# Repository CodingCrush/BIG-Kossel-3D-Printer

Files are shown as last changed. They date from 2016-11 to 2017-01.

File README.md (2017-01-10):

# 项目说明
这个是去年做的3d打印机清单，包括所有非标件及安装示意图。
效应器、两种57挤出机、滑车等非标件均为原创设计，开源供参考使用
按照物料清单买下来，成本2000-2500之内。不同的用料会有不同的成本
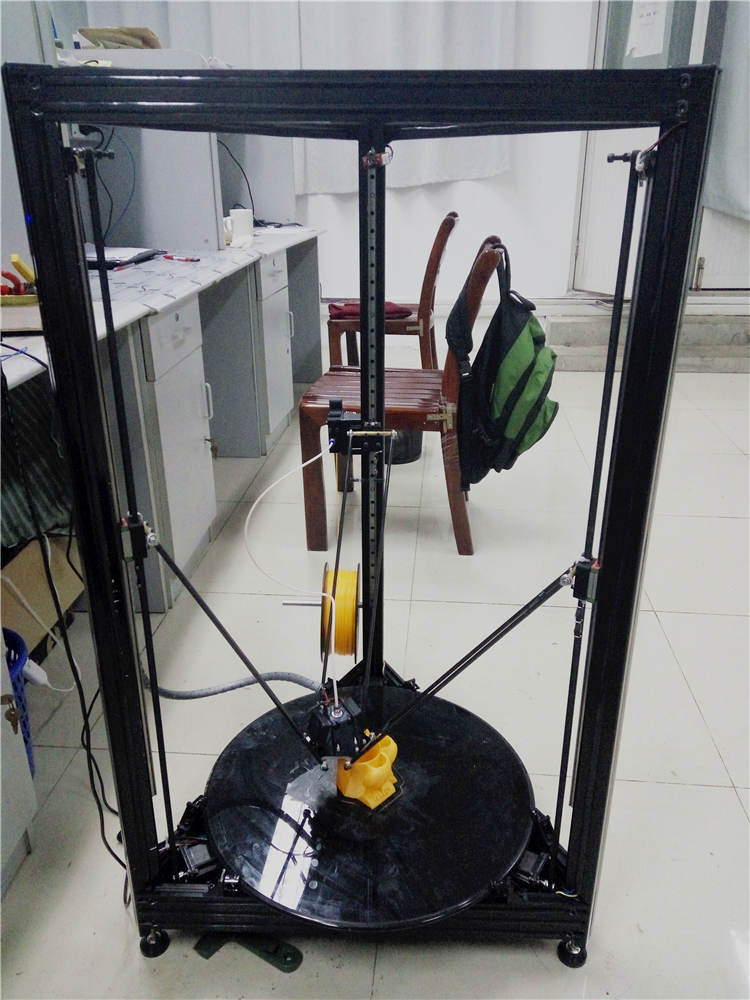
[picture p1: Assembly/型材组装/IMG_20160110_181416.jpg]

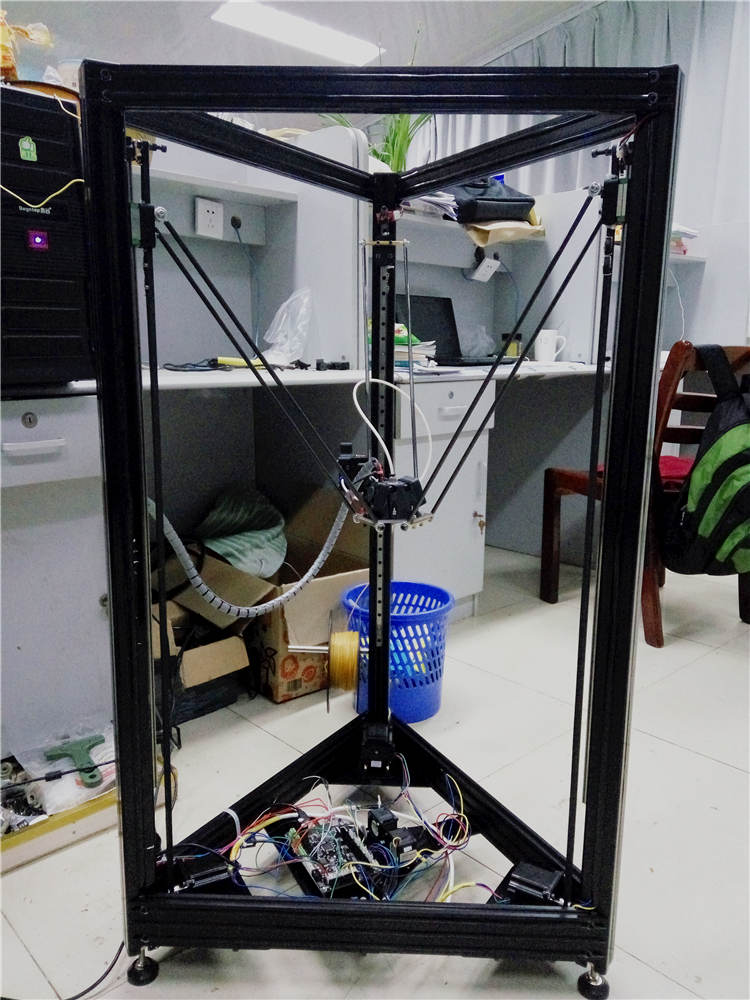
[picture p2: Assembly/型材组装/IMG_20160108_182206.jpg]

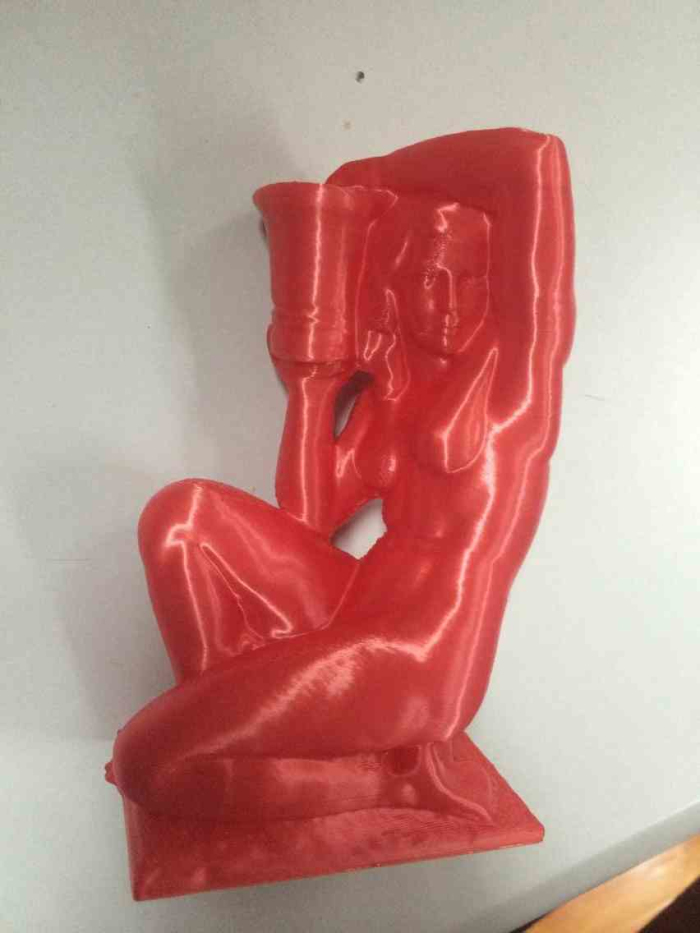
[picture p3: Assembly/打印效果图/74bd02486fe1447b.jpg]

# 成本预算：
框架300
线轨380
主板330
玻璃50
螺丝100
铁板加工件120
亚克力切割件30
轴承50
碳纤维管100
热床（可不选）200
步进电机100
电源50
导线20
其他配件100
齿轮皮带40
其他150
以上邮费200

# 关于效应器：
打印效果确实很棒，出风给喉管和打印件散热。两个12V的4010风扇在24V下超压使用。两侧进风在支架上部的密闭腔体内混合向下送出，密闭腔体相当于静压箱可以降低面风速的湍流度，同时降低面风速。充分保证散热效果。经过四次更新至V2.1版。

# 关于挤出机：
有42电机带韦德挤出与57电机直驱挤出的方案选择。42电机挤出力不够。即使买的行星减速也没那么神奇，不如一步到位，使用57电机直驱。更新至第五版，42mk8---42齿轮行星减速---42皮带减速行星减速---57mk8转接---57bowden。最后发现偷懒省钱都是浪费的开始。57直驱的挤出力强劲，打最小的鸟笼不会拉丝，回抽参数设的为130Mm/s 7mm；

# 挤出机对比
Mk8挤出机的缺点：直齿轮坑料，42电机发热大融料；
42wade齿轮减速挤出机缺点：回抽噪音大，回抽速度不高；
42wade皮带减速挤出机缺点：噪音小，回抽速度依然不高，皮带有可能打滑；
57_mk8挤出机缺点：暂无
57_bowden挤出机缺点：暂无

# 关于成型空间：
我最初做的是1050mm立柱的。打印高度是500mm ，直径是450mm高度。
关于打印效果：
全金属结构保证整机刚性；
32位主板保证运算不顿卡；
堆叠双凤道效应器保证打印件散热强力；
线性导轨保证三轴运动的直线度挤出稳定；
57挤出机保证挤出的力矩和回抽质量；
打印效果和用料息息相关。想省钱又想有好的打印效果是不可能的

# 关于E3D-V6：
请严格安装图上的分开购买，切勿购买套件V6。原版的V6非常容易堵头。
正确安装E3D-V6的方式：
首先将喷嘴拧到加热块上，拧到底，然后回退一圈；
拧上喉管、散热器，用手拧紧，切勿大力，喉管脆弱。容易折断；
联机加热至200度，用扳手固定住加热块，用老虎钳狂拧喷嘴到拧不动为止；
安装教程[参考](http://wiki.e3d-online.com/wiki/E3D-v6_Assembly)：

# 关于固件调试：
我写了三份调试教程：
8位MEGA2560的marlin固件；
32位due的repetier固件；
Mks sbase的smoothieware固件；

配合KOSSEL吧精品帖理解研究

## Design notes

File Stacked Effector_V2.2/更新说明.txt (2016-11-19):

V2.2版本

1.增加30风扇支架
2.取消带走线孔的40风扇支架，加热棒和热敏电阻从效应器下方走线。
3.原E3D固定支架的沉孔不方便在拧螺丝时固定螺母，紧固效果不佳。已经修正
4.使用MGN12H微轨，打印MGN12底座即可。

优点：
我设计的这款双风道效应器实测打印效果很棒。上层的空腔的作用相当于一个静压箱，给两侧进风混合用的，向下出风的面风速湍流度低，散热效果很均匀。试试就不会后悔的
缺点：
必须在切片软件里设置风扇始终运行，第一层风速可以设置的低一点。
不便拆卸。

如果具备加工条件，可以将底座改为铝板+铜柱的设计。铜柱选择M4 50MM长度的，开M3的孔，距离为20mm。

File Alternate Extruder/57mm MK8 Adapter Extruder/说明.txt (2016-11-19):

电机座，带42电机的转接孔，可以安装MK8挤出机或者bowden挤出机
mk8挤出机需要改造齿轮与轴承。直齿轮啃料太过凶猛，所以改造成mk7齿轮和内4外10或12的轴承。
mk8走线管模型是因为mk8从齿轮到进料口的距离太长，高速挤出下容易折弯，所以加入一个螺纹套。减少变形

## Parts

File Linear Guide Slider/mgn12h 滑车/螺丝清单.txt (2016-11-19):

M4 25MM 2个
M3 25MM 4个 及垫片
M4 方螺母2个
M4 铜螺母2个

线轨固定需要
m3 8mm 及20 m3 T螺母 
具体数量自定 

导轨螺孔间距为20mm

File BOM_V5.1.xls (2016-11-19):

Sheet: 安装流程
步序 | 操作
1 | 熟读物料清单；
2 | 确定自己所需机子的高度，根据需求自主提高或降低高度；
3 | 购买铝合金框架、上下铁板连接件、螺丝五金配件等；
4 | 购买线轨；
5 | 制作推杆；
6 | 组装框架线轨玻璃等；
7 | 购买电子配件；
8 | 打印所需非标件；
9 | 再次安装，确定缺少的螺丝数量及长度；
10 | 再次购买螺丝；
11 | 完全安装；
12 | 调试并打印；
所需打印件
滑车 | MGN12滑车 | 3 | 必须需要
 | MGN12滑车盖板 | 3
限位开关 | 9MM/19MM孔距 | 3
2.1版堆叠效应器 | MGN12H底座 | 1
 | E3D支座 | 1
 | 40MM风扇支座 | 2
57_bowden挤出机 | 摇臂 | 1
 | 支座 | 1

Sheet: 框架清单
名称 | 型号 | 数量 | 备注
主体框架
4040氧化黑色欧标铝 | 加工方式见图纸 | 3 | 将铝型材加工图纸发送给客服qq 3307599979，然后购买。大概300元（不含邮费）
2060氧化黑色欧标铝 |  | 3
2040氧化黑色欧标铝 |  | 3
激光切割件，分为两部分
亚克力切割件 | 见图纸 |  | https://item.taobao.com/item.htm?spm=a1z09.2.0.0.DWjkuu&id=20099696260&_u=9b3kpon8ca8 | 大概30元不含邮费
铁板切割件 | BOM默认选择57步进电机底座 |  | https://item.taobao.com/item.htm?spm=a1z09.2.0.0.k5vPzQ&id=40188190385&_u=jb3kpon455d | 大概120元不含邮费
与上面一样，将图纸发给卖家购买
mgn12h线轨套件以及同一家店可以买的
直线导轨MGN12 | 800mm | 3 | https://item.taobao.com/item.htm?spm=a1z09.2.0.0.LKU8Oa&id=26759568854&_u=eb3kpona8c6 | 130一米
导轨滑块 | MGN12H | 3 |  | 28一个
8MM光轴 | 200mm | 1 | https://item.taobao.com/item.htm?spm=a1z10.5-c.w4002-1865926650.40.Pj0TRl&id=18726450513 | 用作料架
光轴支架 | sk8 | 1 | https://item.taobao.com/item.htm?spm=a1z10.5-c.w4002-1865926650.27.MxqcvY&id=18625133704
尼龙定向调节脚 | D40 M8 50MM | 3 | https://item.taobao.com/item.htm?spm=a1z10.5-c.w4002-1865926650.35.BtjLvI&id=38758004319 | 立柱安装的蹄脚
玻璃、固定、以及热床
钢化玻璃平台 | 500mm直径，10mm厚度 | 1 | https://item.taobao.com/item.htm?spm=a1z09.2.0.0.mM9U3M&id=44221134157&_u=ub3kpon85cc
玻璃层夹 | 夹6-10mm玻璃 | 6 | https://item.taobao.com/item.htm?spm=a1z09.2.0.0.mM9U3M&id=16613643636&_u=ub3kpon79ec
玻璃贴膜 | 黑色不透光50X100 | 1 | https://item.taobao.com/item.htm?spm=a1z09.12.0.0.oPNmCq&id=35529763436&_u=eb3kpon4e8c
固体胶 | 7092固体胶 | 1 | https://detail.tmall.com/item.htm?spm=a230r.1.14.15.UjnPbe&id=521067459509&ns=1&abbucket=19
硅橡胶加热板热床 | D=450MM | 1 | https://item.taobao.com/item.htm?spm=a1z09.2.0.0.JIdvOC&id=524124462678&_u=eb3kpon2f34
热床200包邮，我买的是220V 150W的固定功率热床，表面温度大概可以达到60摄氏度。根据经济实力决定是否购买
推杆、轴承 |  |  |  | 外部可以套上彩色热缩管
铝管 | 内径4MM 外径 6MM,450MM长度 | 6 | https://item.taobao.com/item.htm?spm=a1z09.2.0.0.ZB8lGC&id=41292505365&_u=1b3kpond9cf
碳纤维管 | 内径4MM 外径 6MM,450MM长度 | 6 | https://item.taobao.com/item.htm?spm=a1z09.2.0.0.V9akuZ&id=38251842903&_u=eb3kpon99a4 | 用AB胶固定
铝管大概20块，碳纤维大概100块。一个不好看不抗弯，一个好看抗弯。根据经济实力决定买哪个
挤出机用轴承 | 608ZZ | 1 | https://item.taobao.com/item.htm?spm=a1z10.3-c.w1017-2093055617.16.R8DyGV&id=16485904719&
鱼眼杆端关节轴承 | SA4/T | 12 | https://item.taobao.com/item.htm?spm=a1z10.3-c.w1017-2093055617.54.vsEDZy&id=16076773170&
惰轮用法兰轴承 | MF105ZZ | 6 | https://item.taobao.com/item.htm?spm=a1z10.3-c.w1017-2093055617.48.7UzuTb&id=21102608035&
线材以及同一家店可以买到的
导线 | 黑黄蓝红 | 各5m | https://item.taobao.com/item.htm?spm=a1z09.2.0.0.0SBSik&id=23540708099&_u=eb3kpon026b
XH2.54接插件 | 2P | 1 | https://item.taobao.com/item.htm?spm=a1z09.2.0.0.0SBSik&id=14476357944&_u=eb3kpone20c
 | 3P | 1 | https://item.taobao.com/item.htm?spm=a1z09.2.0.0.0SBSik&id=14473394032&_u=eb3kponfa8b
 | 4P | 1 | https://item.taobao.com/item.htm?spm=a1z10.3-c.w4002-12998195972.51.XmKiKG&id=14476473424
热缩管 | 3mm直径 | 5m | https://item.taobao.com/item.htm?spm=a1z10.3-c.w4002-12998195972.12.nhstYa&id=13996979237
电源插头 | 2脚 | 1 | https://item.taobao.com/item.htm?spm=a1z10.3-c.w4002-12998195972.80.4smjrb&id=20905900482
AB胶 |  | 1 | https://item.taobao.com/item.htm?spm=a1z10.3-c.w4002-12998195972.9.vEEsrS&id=36276164986

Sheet: 配件清单
名称 | 型号 | 数量 | 链接 | 备注
电源
24V开关电源 | 24V 4.5A | 1 | https://detail.tmall.com/item.htm?id=37030219054&ali_trackid=1_5102b68adeeb74cf0f9209195d0a94c7
32位主板方案
MKS SBASE V1.1 | SMOOTHIEBOARD | 1 | https://item.taobao.com/item.htm?spm=a230r.1.14.9.vgDiJN&id=44718074273&ns=1&abbucket=15#detail | 推荐用32位，8位效果不行。一步到位不要瞎折腾
显示屏 | 12864 | 1 | https://item.taobao.com/item.htm?spm=a1z10.5-c.w4002-3498108424.13.ABPwxh&id=36373394177
显示屏延长线 | 10pin 60cm | 1 | https://item.taobao.com/item.htm?spm=a1z10.3-c.w4002-3498109524.9.ptclZO&id=40086051115
E3D-V6 1.75mm 喷头套件
喉管 | 4.1改进版 | 1 | https://item.taobao.com/item.htm?spm=a1z10.5-c.w4002-11935848136.17.evg1rh&id=44465372886 | 不建议购买E3DV6套件，价格贵并且还需要单独改造
喷嘴 | 一般为1.75MM/0.4 | N | https://item.taobao.com/item.htm?spm=a1z10.5-c.w4002-11935848136.34.nrbVxR&id=44358306425 | 喷嘴属于易耗品，建议买三四个备用
加热块 | E3D-V6 | 1 | https://item.taobao.com/item.htm?spm=a1z0d.6639537.1997196601.16.l5Cwhh&id=42040453133
V6散热器 | 远程通用 | 1 | https://item.taobao.com/item.htm?spm=a1z0d.6639537.1997196601.24.l5Cwhh&id=44405326311
12V 40W 加热棒 | 24V | 1 | https://item.taobao.com/item.htm?spm=a1z0d.6639537.1997196601.32.l5Cwhh&id=40297664127
热敏电阻 | NTC 100k | 1 | https://item.taobao.com/item.htm?spm=a1z0d.6639537.1997196601.40.l5Cwhh&id=40254167255
直通快拆 |  | 1 | https://item.taobao.com/item.htm?spm=a1z0d.6639537.1997196601.56.l5Cwhh&id=42054728629 | 必须要，可有效减少拉丝
普通快拆 | PC4-M6 | 1 | https://item.taobao.com/item.htm?spm=a1z10.3-c.w4002-11935848131.29.ZmzM5A&id=520893975535
57挤出机
步进电机 | 57/出轴8MM | 1 | https://item.taobao.com/item.htm?spm=a1z0d.6639537.1997196601.4.DnqXQb&id=40165378221
步进电机支座 | 57 | 1 | https://item.taobao.com/item.htm?spm=a1z10.3-c.w1017-2775512882.16.UAF9zR&id=40276550667&
42步进电机
步进电机减震器 | 42步进电机减震 | 1 | https://item.taobao.com/item.htm?spm=a1z10.3-c.w4002-5542399676.10.WlW5mC&id=41871297943
步进电机 | 42 | 3 | https://item.taobao.com/item.htm?spm=a1z0d.6639537.1997196601.198.3fQ353&id=520141390607 | 要求拆除带轮
8MM挤出齿轮以及皮带
mk7 齿轮 | 1.75/内孔8MM | 1 | https://item.taobao.com/item.htm?spm=a230r.1.14.73.4LRCcv&id=43350287703&ns=1&abbucket=17#detail
皮带 | 2gt/6mm | 7m | https://item.taobao.com/item.htm?spm=a1z10.5-c.w4002-4073923749.44.Nxt9Df&id=35878681904
其他配件
皮带张力弹簧 |  | 10 | https://item.taobao.com/item.htm?spm=a1z09.2.0.0.ZB8lGC&id=40715365020&_u=1b3kpond30a | 一次装一个，多6个备用，用久了弹力损失
拉杆弹簧 |  | 10 | https://item.taobao.com/item.htm?spm=a1z09.2.0.0.ZB8lGC&id=44068679730&_u=1b3kponee4c | 中间拉成范性形变，否则力道太大，拉杆会变形
散热风扇 | 4010 | 5 | https://item.taobao.com/item.htm?spm=a1z09.2.0.0.ZB8lGC&id=40335881133&_u=1b3kpon0285 | 2个做效应器，2个吹主板，剩1个吹挤出机或备用
四氟管 | PTFE 内2 外4 | 1m | https://item.taobao.com/item.htm?spm=a1z10.3-c.w4002-11935848131.19.E6PGeQ&id=44357906558
降压模块 | LM2596 | 1 | https://item.taobao.com/item.htm?spm=a1z0d.6639537.1997196601.41.zaBsTh&id=40019604731 | 吹主板的风扇降压，24V IN ，12V out。工作在24V太吵。效应器风扇则需要超压使用，否则风力不足
挤出机弹簧 |  | 3 | https://item.taobao.com/item.htm?spm=a1z09.2.0.0.udr64W&id=42750895769&_u=nb3kpon16d7
限位开关 | 19mm孔距 | 3 | https://item.taobao.com/item.htm?spm=a1z09.2.0.0.iTCYy6&id=39937698796&_u=eb3kpon373c
步进电机支座 | 42 | 3 | https://item.taobao.com/item.htm?spm=a1z10.3-c.w4002-11935848131.9.PmEVYh&id=39937902501
2gt同步带轮 | 16齿/5mm | 3 | https://item.taobao.com/item.htm?spm=a1z10.3-c.w4002-11935848131.11.RbJe5L&id=39890812501
包邮类
绕线管 | 黑色 | https://item.taobao.com/item.htm?spm=a230r.1.14.38.aUPH6V&id=45706578890&ns=1&abbucket=8#detail
主板TF卡 | 2g | https://item.taobao.com/item.htm?spm=a230r.1.14.1.p7Qztg&id=524953996445&ns=1&abbucket=8#detail
USB打印线 | 3m | https://detail.tmall.com/item.htm?id=10923587984&cm_id=140105335569ed55e27b&abbucket=8&skuId=50238254065
自喷漆 | 黑色 | https://detail.tmall.com/item.htm?id=520129085679&cm_id=140105335569ed55e27b&abbucket=8&skuId=3100609580236
铲刀 | BT-L120 | https://detail.tmall.com/item.htm?id=45471830184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

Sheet: 螺丝清单
40&20型材间连接，以下内六角螺丝基本在宇昊通五金店都能找到
M5 14MM | 24 | https://item.taobao.com/item.htm?spm=a1z09.2.0.0.Be0ikY&id=16463536281&_u=eb3kponf473
40_M5滑块螺母 | 24 | https://item.taobao.com/item.htm?spm=a1z09.2.0.0.Be0ikY&id=15146235453&_u=eb3kpon8b90
MGN12H固定，注意摆放居中。小心安装，槽宽较大。40_M3螺母奇货可居
M3 12MM | 15
40_m3滑块螺母 | 15 | https://buyertrade.taobao.com/trade/itemlist/list_bought_items.htm?spm=2013.1.1997525045.2.vBxTNu
玻璃固定
2028角码 | 6 | 一共固定6个玻璃层夹
M5 10MM | 12
20_M5_T螺母 | 6
M5螺母 | 6
M5 垫片 | 18
57_bowden挤出机
M3 50MM | 1 | 螺丝、挤出臂、电机座、弹簧、螺母依次固定。抗弯用
M5 8MM | 2
M4 50MM | 4 | 固定到电机座上，其中右上角固定时中间加一弹簧
M8 16MM圆柱销 | 1 | https://item.taobao.com/item.htm?spm=a1z09.2.0.0.49Pr58&id=37496544497&_u=eb3kpon8f8e
M4 25MM | 2
PC4-M6扁螺母 | 2 | https://item.taobao.com/item.htm?spm=a1z09.2.0.0.49Pr58&id=38609743045&_u=eb3kponab8b
M4 50蝶形螺丝 | 2 | https://item.taobao.com/item.htm?spm=a1z09.2.0.0.49Pr58&id=39064367809&_u=eb3kpon3ad6
40_M4_T螺母 | 2 | 固定电机座
M4 10MM | 2
M4方螺母 | 4
42_步进电机
M4 12MM | 12 | 固定步进电机座到铁板上
M4螺母 | 12
M5 8MM | 12 | 固定铁板到20型材上
20_M5_T螺母 | 12
M3 12MM | 6 | 固定减震垫到电机座上
M3螺母 | 6
M3 10MM | 6 | 固定步进电机到减震垫上
惰轮的固定
2028角码 | 3 | 把角码固定在铁板上
M5 10MM | 3
M5螺母 | 3
M5 8MM | 12 | 固定铁板到20型材上
20_M5_T螺母 | 12
M5 50MM 全牙 | 3 | https://item.taobao.com/item.htm?spm=a1z10.3-c.w4002-9022202682.74.5PrEE9&id=16566972853
M5螺母 | 18 | 固定长螺丝
线轨滑车铜柱版和非铜柱版共同所需螺丝 |  |  | 铜柱需要自己加工打孔，间距为20mm，打孔M3
M4 20MM | 6
M4方螺母 | 6 | M4*7*2(碳钢镀彩锌)
M3 25MM | 12 | 加垫片
M3 20mm | 6
M4铜螺母 | 6 | https://item.taobao.com/item.htm?spm=a1z10.3-c.w4002-9022202682.35.IZaODN&id=4394094562
M4 40MM双通铜柱 | 6 | https://item.taobao.com/item.htm?spm=a1z10.3-c.w4002-12153267213.26.eVsX5I&id=44046619758
堆叠式效应器铜柱版和非铜柱版共同所需螺丝
M4 20MM | 6 | 固定鱼眼
M4铜螺母 | 6
M4方螺母 | 6
M3 50MM | 2 | 固定两片E3D支座
M3 25MM | 4 | 固定E3D支座
M3 15MM | 8 | 固定4010风扇
M3 15MM | 4 | 固定风扇支架
M3螺母 | 4 | 风扇支架卡住的螺丝
M4 50MM双通铜柱 | 6 | https://item.taobao.com/item.htm?spm=a1z10.3-c.w4002-12153267213.26.eVsX5I&id=44046619758
主板及亚克力固定所需螺丝
M5 8MM | 3 | 固定亚克力到20型材上
20_M5_T螺母 | 3
M3*6+6单通铜柱 | 6 | https://item.taobao.com/item.htm?spm=a1z10.3-c.w4002-9022202682.9.PBuRxQ&id=14854113926
M3螺母 | 12 | 固定铜柱到亚克力板上
M3 8MM | 6 | 固定主板和降压板到铜柱上
2028角码 | 1 | 固定风扇支架到亚克力上
M5 10MM | 2
M5螺母 | 2
M3 20MM | 8 | 固定风扇到风扇支架上
M3螺母 | 8
限位开关固定
30_M4_T螺母 | 3 | 固定限位开关支座到40型材上
M4 10MM | 3
M3 8MM | 6 | 固定限位开关到支座上
装饰平封条
20系列平封条 | 18m | https://item.taobao.com/item.htm?spm=a1z09.2.0.0.ZB8lGC&id=43861741264&_u=1b3kpon28bf
黑色40系列平封条 | 10m | https://item.taobao.com/item.htm?spm=a1z09.2.0.0.49Pr58&id=43825390300&_u=eb3kpon36ad
4040盖板 | 3 | https://item.taobao.com/item.htm?spm=a1z09.2.0.0.iTCYy6&id=41300397509&_u=eb3kpon2bbd

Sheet: 42wade(供参考)
名称 | 型号 | 数量 | 链接 | 备注
绞丝轴 |  | 1 | https://item.taobao.com/item.htm?spm=a1z09.2.0.0.udr64W&id=40386340875&_u=nb3kpona52b
弹簧 |  | 2 | https://item.taobao.com/item.htm?spm=a1z09.2.0.0.udr64W&id=42750895769&_u=nb3kpon16d7
轴承 | 608ZZ | 3 | https://item.taobao.com/item.htm?spm=a1z09.2.0.0.udr64W&id=42879447860&_u=nb3kpon72ef
无头机米螺丝 | M4 10MM | 2 | https://item.taobao.com/item.htm?spm=a1z0d.6639537.1997196601.34.n9pQzp&id=36267353233 | 固定电机小齿轮
螺母 | M4 | 2
 | M3 20MM | 3 |  | 固定42电机
 | M3 25MM | 1
 | M3 螺母 | 1 |  | 固定摇柄
 | M4 60MM | 2 |  | 固定弹簧
 | M4扁螺母或方螺母 | 2
 | M4蝶形螺母 | 2 | https://item.taobao.com/item.htm?spm=a1z0d.6639537.1997196601.44.n9pQzp&id=35480309874
 | M8 螺母 | 1
 | 扁M6 螺母 | 1 | https://item.taobao.com/item.htm?spm=a1z0d.6639537.1997196601.64.n9pQzp&id=37376708205 | 固定PC4-M6
圆柱销 | m8 16MM | 1 | https://item.taobao.com/item.htm?spm=a1z0d.6639537.1997196601.14.n9pQzp&id=35470507276
推荐使用57直驱挤出机，该方案供已有42电机作挤出机的使用。因为42电机扭矩不足，直驱容易失步，所以需要齿轮减速
42步进电机 | 身长不限，用作挤出机 | 1 | 韦德挤出机
42电机支座 |  | 1 | https://item.taobao.com/item.htm?spm=a1z09.2.0.0.ZB8lGC&id=39937902501&_u=1b3kpon197f | 固定挤出机

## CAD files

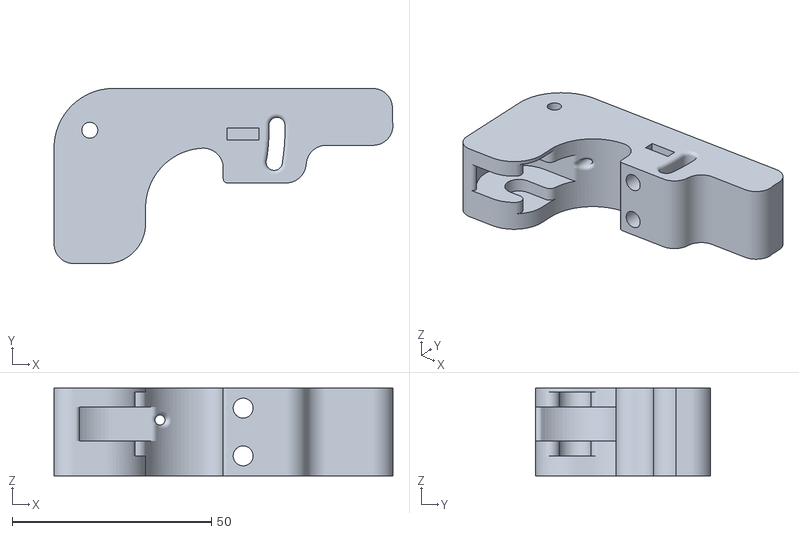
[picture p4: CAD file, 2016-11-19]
57mm Bowden Extruder/挤出臂，走线偏离中心3mm.stl
85.1 x 44.0 x 22.0

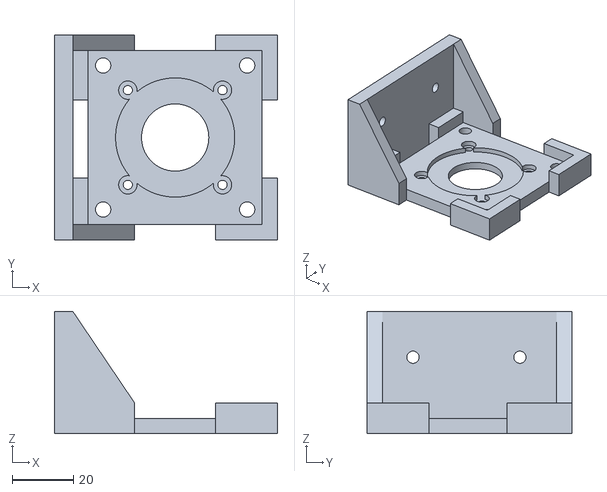
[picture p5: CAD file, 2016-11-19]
Alternate Extruder/57mm MK8 Adapter Extruder/57电机座.stl
73.0 x 67.0 x 40.0

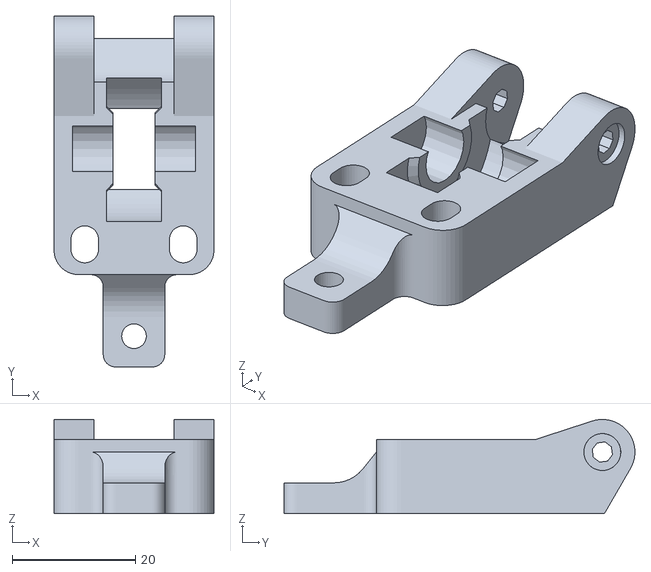
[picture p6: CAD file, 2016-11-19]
Alternate Extruder/Improved 42mm Wade Extruder/M4_Guidler_2.stl
26.0 x 57.0 x 15.3

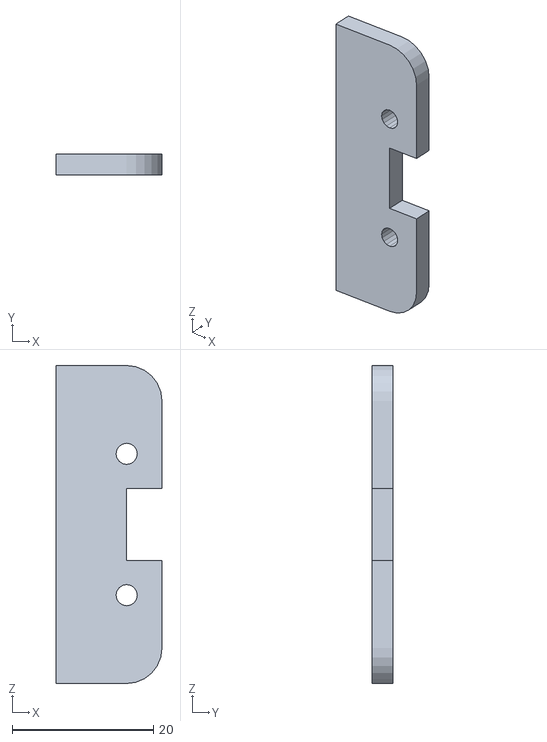
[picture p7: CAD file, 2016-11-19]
Linear Guide Slider/mgn12h 滑车/mgn12h_盖板.stl
15.0 x 3.00 x 45.0

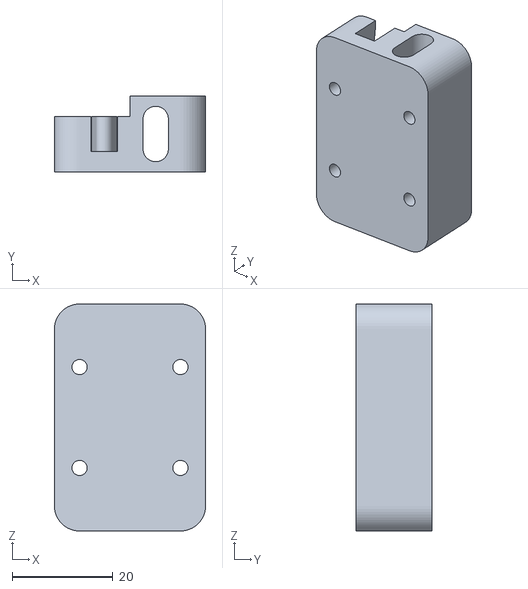
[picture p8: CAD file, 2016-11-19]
Linear Guide Slider/mgn12h滑车（需配合铜柱）/mgn12h_carriage.stl
30.0 x 15.0 x 45.0

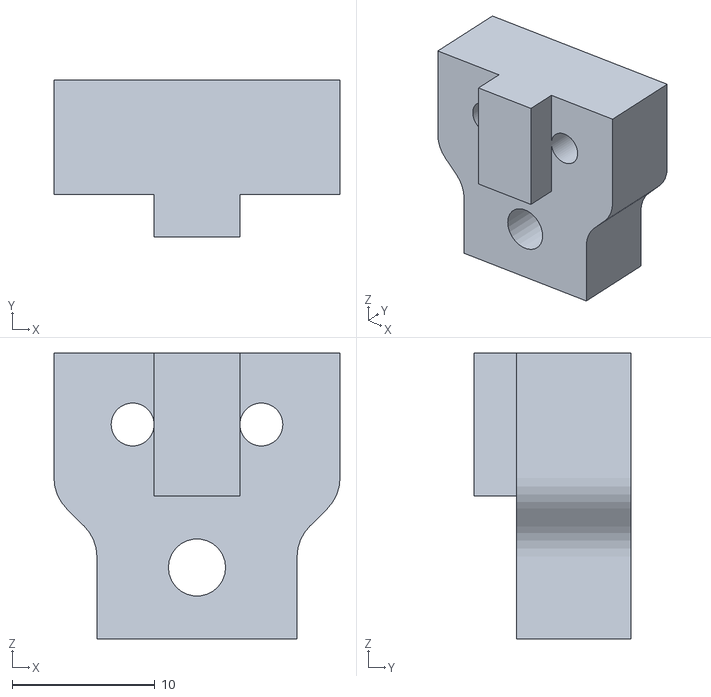
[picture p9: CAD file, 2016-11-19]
Mechanical Limit Switch Holder/mgn12h_9mm.stl
20.0 x 11.0 x 20.0

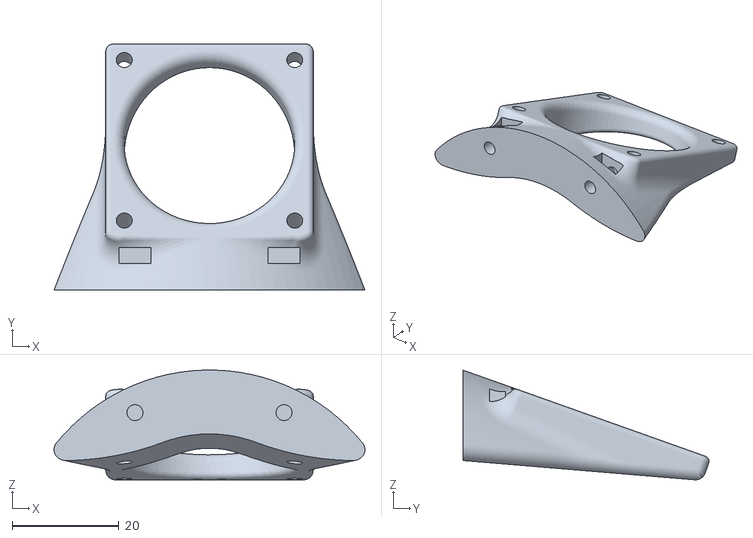
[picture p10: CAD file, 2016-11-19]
Stacked Effector_V2.2/40风扇支架.stl
58.4 x 46.2 x 20.6

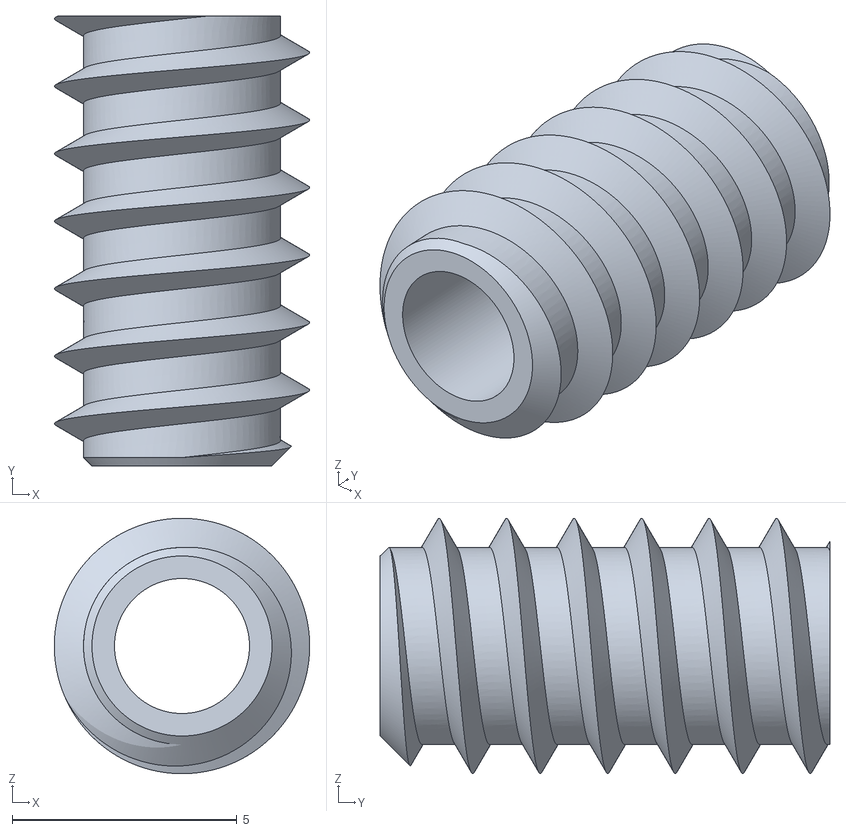
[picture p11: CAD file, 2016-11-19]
Alternate Extruder/57mm MK8 Adapter Extruder/M6螺纹套.stl
5.68 x 10.0 x 5.68

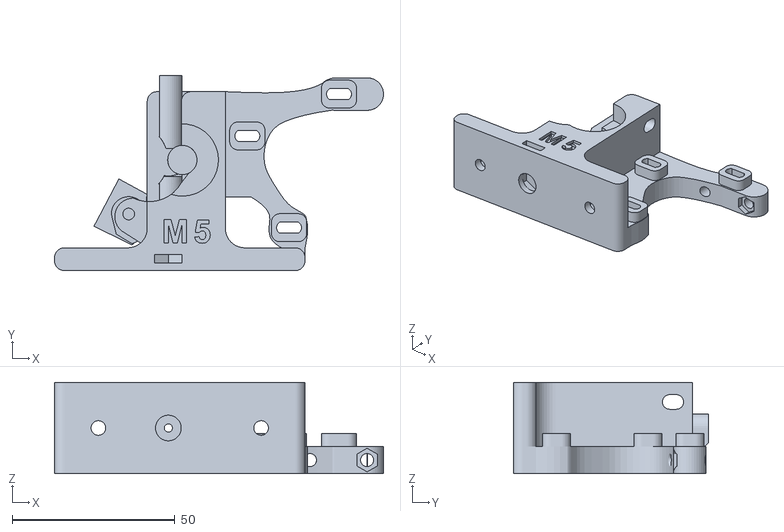
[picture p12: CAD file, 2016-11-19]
Alternate Extruder/Improved 42mm Wade Extruder/extruder_bowdenM5.stl
101.1 x 60.0 x 28.0

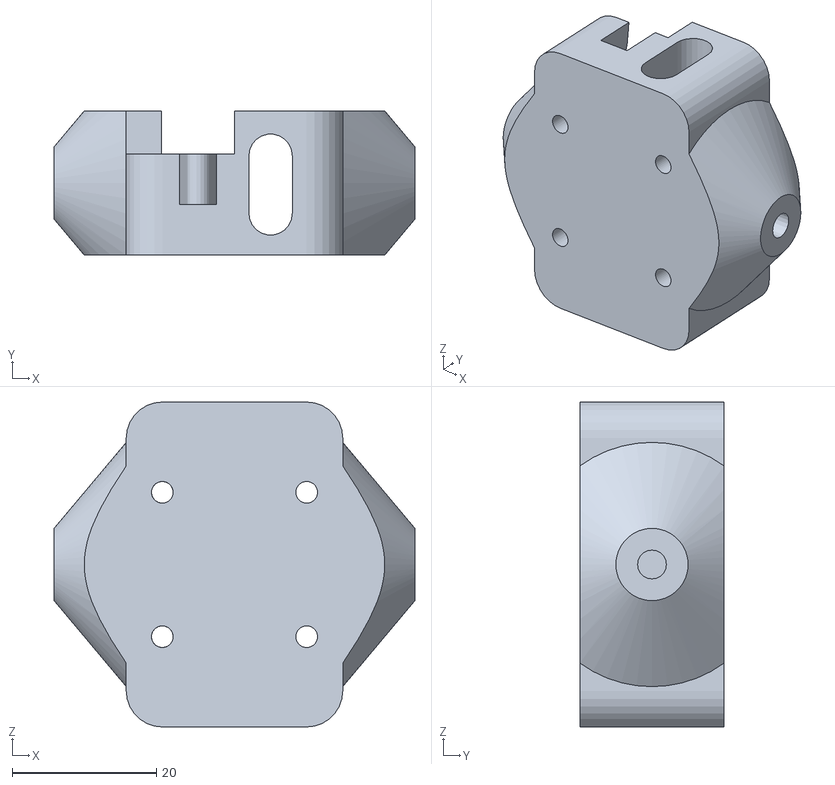
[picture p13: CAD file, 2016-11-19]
Linear Guide Slider/mgn12h 滑车/mgn12h_滑车.stl
50.0 x 20.0 x 45.0

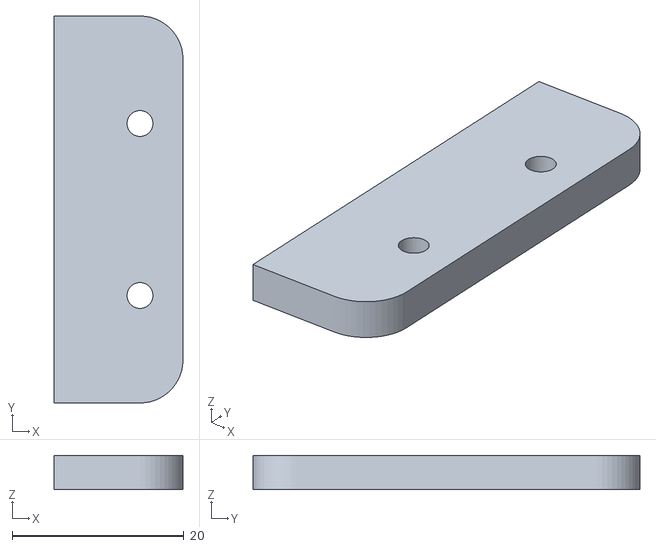
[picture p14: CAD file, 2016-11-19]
Linear Guide Slider/mgn12h滑车（需配合铜柱）/gaiban.stl
15.0 x 45.0 x 4.00

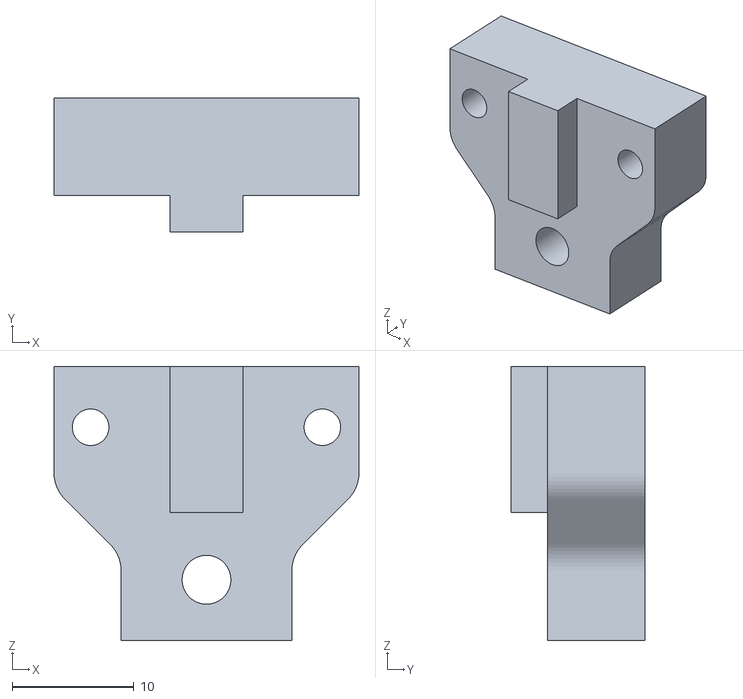
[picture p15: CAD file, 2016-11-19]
Mechanical Limit Switch Holder/mgn12h_19mm.stl
25.0 x 11.0 x 22.5

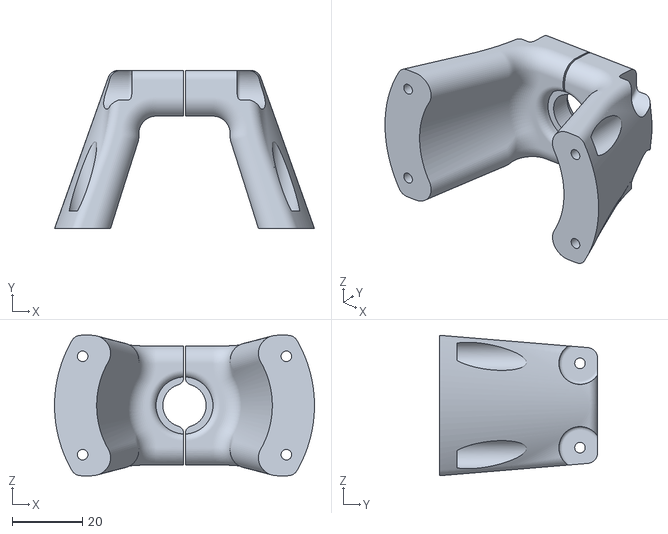
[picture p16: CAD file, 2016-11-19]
Stacked Effector_V2.2/E3D支座.stl
74.0 x 45.0 x 40.0

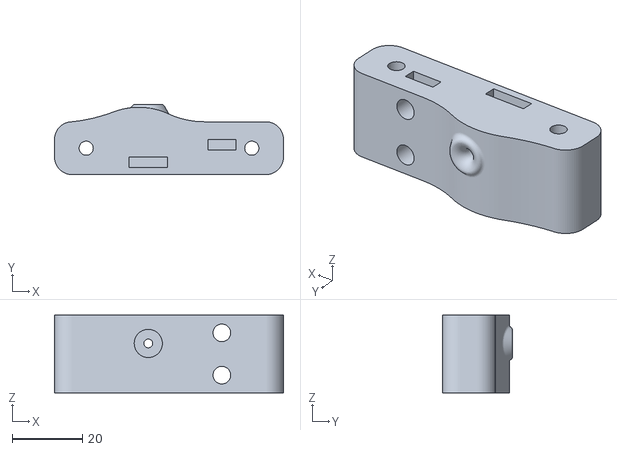
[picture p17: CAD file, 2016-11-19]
57mm Bowden Extruder/支座，走线偏离中心3mm.stl
65.0 x 19.9 x 22.0

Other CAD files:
Frame/激光切割件图纸.dwg
Frame/型材加工图纸.dwg
Alternate Extruder/57mm MK8 Adapter Extruder/40风扇架.stl
Alternate Extruder/Improved 42mm Wade Extruder/韦德挤出机人字齿轮.stl
57mm Bowden Extruder/M8 16MM圆柱销.stl
Alternate Extruder/Improved 42mm Wade Extruder/M4_Guidler_3.STL
Alternate Extruder/Improved 42mm Wade Extruder/big_gear.STL
Alternate Extruder/Improved 42mm Wade Extruder/extruder_bowdenM6.stl
Alternate Extruder/Improved 42mm Wade Extruder/small_gear_M4_nut.stl
Stacked Effector_V2.2/30风扇支架.stl
Stacked Effector_V2.2/MGN12H底座，鱼眼间距50mm.stl

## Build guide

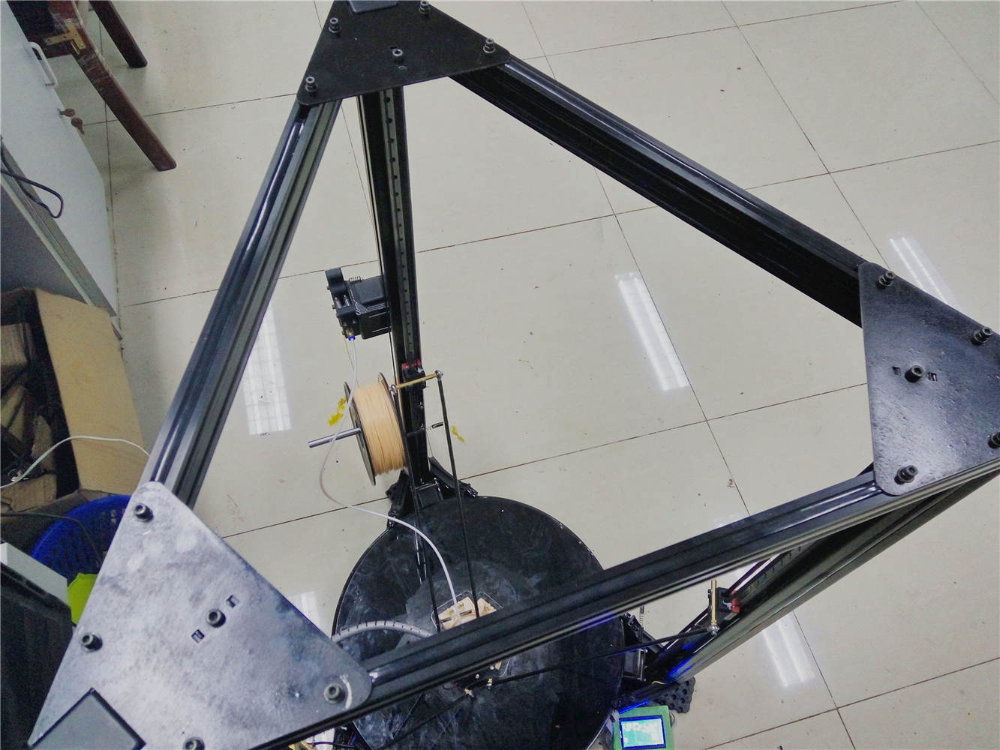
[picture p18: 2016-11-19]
Assembly/图：玻璃及惰轮固定/IMG_20160113_211552_HDR.jpg

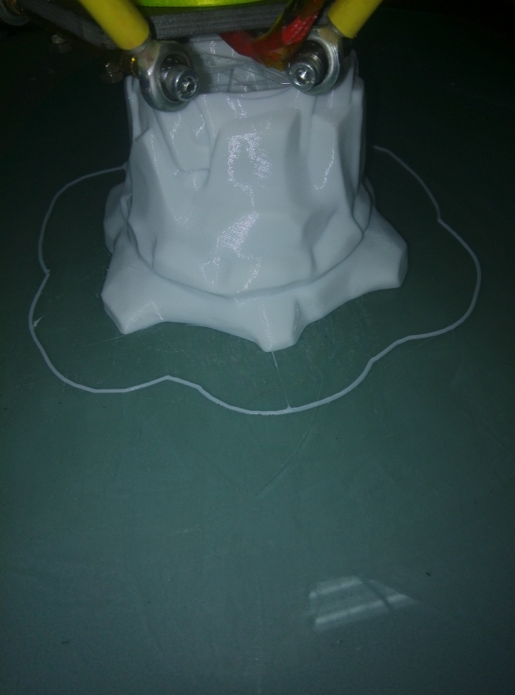
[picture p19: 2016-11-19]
Assembly/打印效果图/IMG20151101184557.jpg

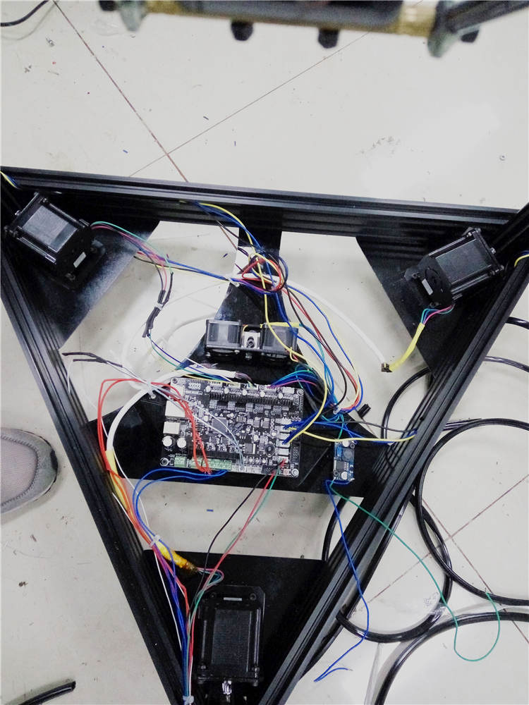
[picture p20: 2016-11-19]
Assembly/电机及减震垫固定/IMG20160108173014.jpg

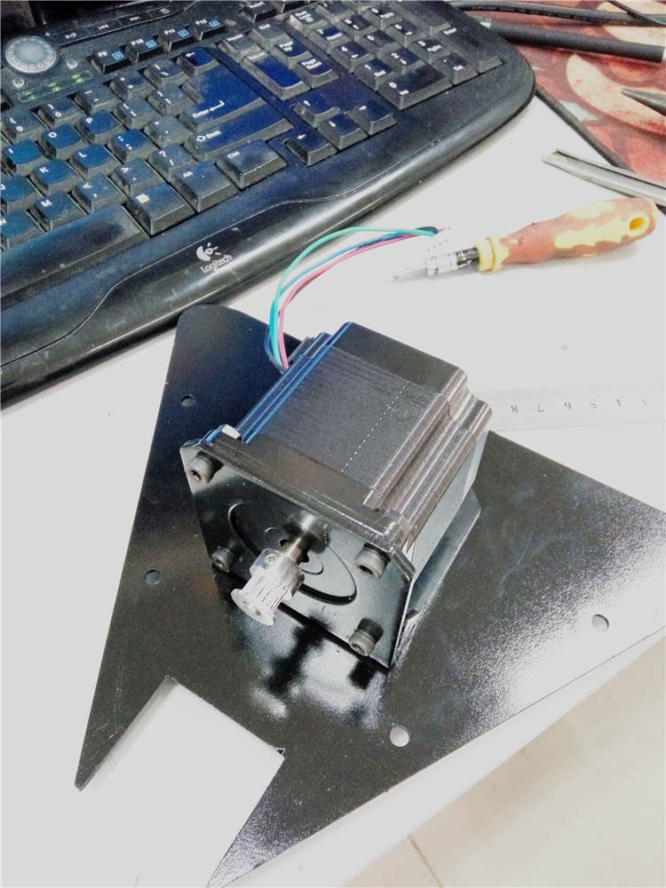
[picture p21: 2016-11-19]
Assembly/电机及减震垫固定/IMG_20160107_141122.jpg

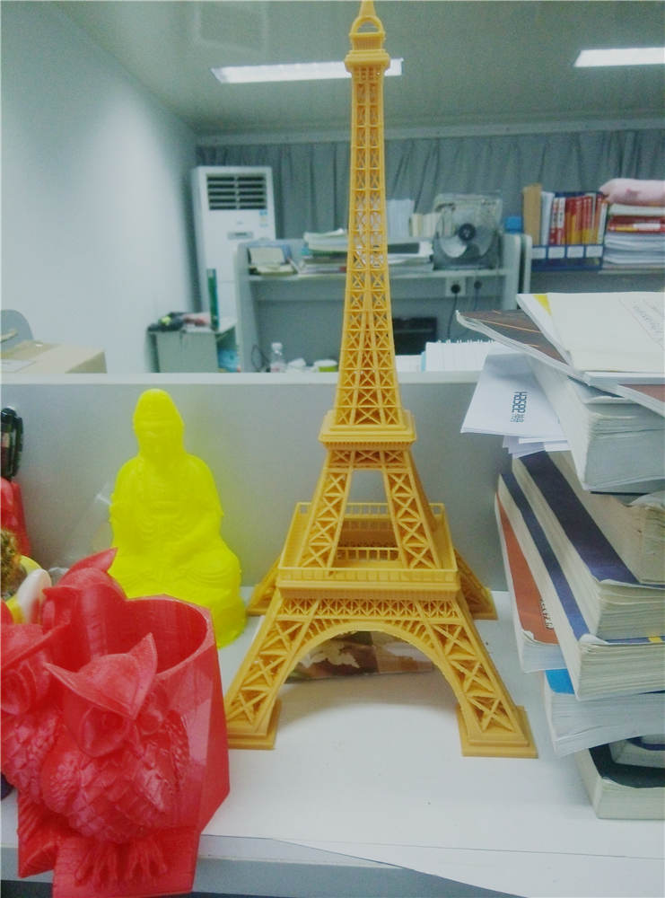
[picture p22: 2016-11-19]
Assembly/打印效果图/IMG20151224100719.jpg

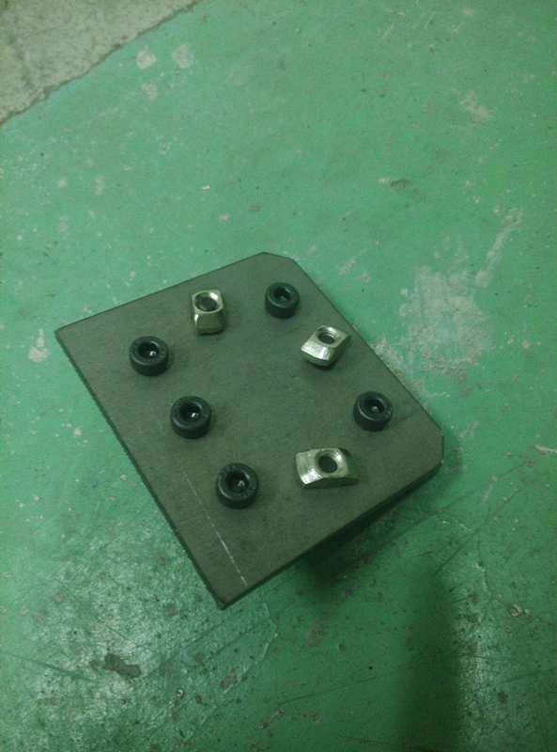
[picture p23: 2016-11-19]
Assembly/图：推杆制作/IMG_20150901_211314.jpg

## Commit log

2016-11-19 Init push
    [30风扇支架.stl, 40风扇支架.stl, 40风扇架.stl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]
2017-01-10 Rename projects directory
    [30风扇支架.stl, 40风扇支架.stl, 40风扇架.stl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]
2017-01-10 fix error
    [gaiban.stl, mgn12h_carriage.stl, mgn12h_滑车.stl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]
